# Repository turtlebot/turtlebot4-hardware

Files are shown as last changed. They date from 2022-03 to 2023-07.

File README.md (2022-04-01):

# Turtlebot4 Hardware

<table>
    <thead>
        <tr>
            <th>Feature</th>
            <th>
                TurtleBot 4 Lite
            </th>
            <th>
                TurtleBot 4
            </th>
        </tr>
    </thead>
    <tbody>
        <tr>
            <td>Size (L x W x H)</td>
            <td>342 x 339 x 192 mm</td>
            <td>342 x 339 x 351 mm</td>
        </tr>
        <tr>
            <td>Weight</td>
            <td>3270 g</td>
            <td>3945 g</td>
        </tr>
        <tr>
            <td>Base platform</td>
            <td>iRobot® Create® 3</td>
            <td>iRobot® Create® 3</td>
        </tr>
        <tr>
            <td>Wheels (Diameter)</td>
            <td>72 mm</td>
            <td>72 mm</td>
        </tr>
        <tr>
            <td>Ground Clearance</td>
            <td>4.5 mm</td>
            <td>4.5 mm</td>
        </tr>
        <tr>
            <td>On-board Computer</td>
            <td>Raspberry Pi 4B 4GB</td>
            <td>Raspberry Pi 4B 4GB</td>
        </tr>
        <tr>
            <td>Maximum linear velocity	</td>
            <td>0.31 m/s in safe mode, 0.46 m/s without safe mode</td>
            <td>0.31 m/s in safe mode, 0.46 m/s without safe mode</td>
        </tr>
        <tr>
            <td>Maximum angular velocity</td>
            <td>1.90 rad/s</td>
            <td>1.90 rad/s</td>
        </tr>
        <tr>
            <td>Maximum payload	</td>
            <td>9 kg</td>
            <td>9 kg</td>
        </tr>
        <tr>
            <td>Operation time	</td>
            <td>2h 30m - 4h depending on load</td>
            <td>2h 30m - 4h depending on load</td>
        </tr>
        <tr>
            <td>Charging time</td>
            <td>2h 30m</td>
            <td>2h 30m</td>
        </tr>
        <tr>
            <td>Bluetooth Controller</td>
            <td>Not Included</td>
            <td>TurtleBot 4 Controller</td>
        </tr>
        <tr>
            <td>Lidar</td>
            <td>RPLIDAR A1M8</td>
            <td>RPLIDAR A1M8</td>
        </tr>
        <tr>
            <td>Camera</td>
            <td>OAK-D-Lite</td>
            <td>OAK-D-Pro</td>
        </tr>
        <tr>
            <td>User Power</td>
            <td>
                VBAT @1.9A <br/>
                5V @ Low current <br/>
                3.3V @ Low current
            </td>
            <td>
                VBAT @ 300 mA <br/>
                12V @ 300 mA <br/>
                5V @ 500 mA <br/>
                3.3v @ 250 mA
            </td>
        </tr>
        <tr>
            <td>USB Expansion</td>
            <td>
                USB 2.0 (Type A) x2 <br/>
                USB 3.0 (Type A) x2
            </td>
            <td>
                USB 2.0 (Type A) x2 <br/>
                USB 3.0 (Type A) x1 <br/>
                USB 3.0 (Type C) x4
            </td>
        </tr>
        <tr>
            <td>Programmable LEDs</td>
            <td>Create® 3 Lightring</td>
            <td>
                Create® 3 Lightring <br/>
                User LED x2
            </td>
        </tr>
        <tr>
            <td>Status LEDs</td>
            <td>-</td>
            <td>
                Power LED <br/>
                Motors LED <br/>
                WiFi LED <br/>
                Comms LED <br/>
                Battery LED
            </td>
        </tr>
        <tr>
            <td>Buttons and Switches</td>
            <td>
                Create® 3 User buttons x2 <br/>
                Create® 3 Power Button x1
            </td>
            <td>
                Create® 3 User buttons x2 <br/>
                Create® 3 Power Button x1 <br/>
                User Buttons x4
            </td>
        </tr>
        <tr>
            <td>Battery</td>
            <td>26 Wh Lithium Ion (14.4V nominal)</td>
            <td>26 Wh Lithium Ion (14.4V nominal)</td>
        </tr>
        <tr>
            <td>Charging Dock</td>
            <td>Included</td>
            <td>Included</td>
        </tr>
    </tbody>
</table>

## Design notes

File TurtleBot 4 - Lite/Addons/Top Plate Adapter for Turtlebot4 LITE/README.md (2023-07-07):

# Top Plate Adapter for Turtlebot4 LITE

These adapter plates allow easy attachment of additional components without making permanent modificaitons to the Create3 base. This adapter plate has been designed to be compatible with the Turtlebot4 Standard Top Plate. The fastener locations can be altered as needed.

Use of this adapter plate requires some additional hardware components. Suggested hardware is linked from Mcmaster Carr but substitutions that match the part specifications will work as well. 

# Component List

| Description | Quantity | Mcmaster Carr Equivalent |
|:---|:---|---|
| Threaded Insert, Heat Set—M4×0.7 8mm Long, Brass | 4 | 94180A353 |
| Screw, Cap, Round Head—M3×0.5 X 10, Stainless Steel Type 18-8 | 4 | 92095A182 |
| Nut, Hex—M3×0.5, Stainless Steel Type 18-8 | 4 | 91828A211 |
| Washer, Flat—Ø3.2 X Ø7 X 0.6, Stainless Steel Type 18-8 | 4 | 93475A210 |

installed_adapter_plate

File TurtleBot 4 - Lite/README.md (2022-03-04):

# Turtlebot4 Lite

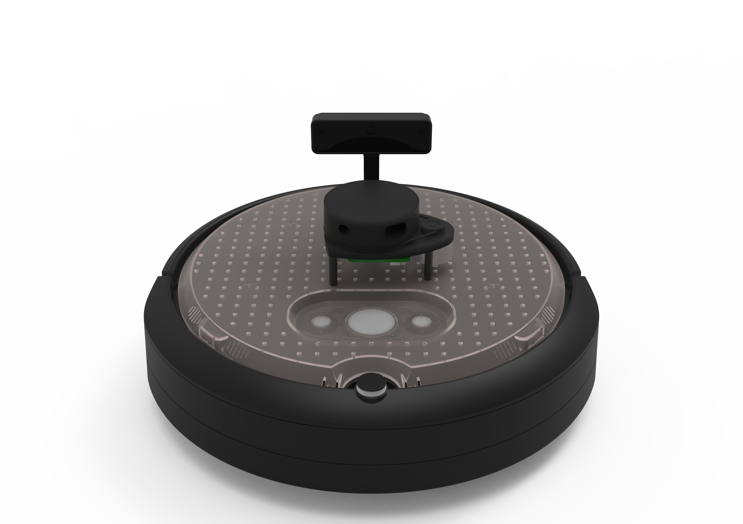
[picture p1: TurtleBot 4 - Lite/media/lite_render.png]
turtlebot4_lite


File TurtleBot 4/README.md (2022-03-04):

# Turtlebot4

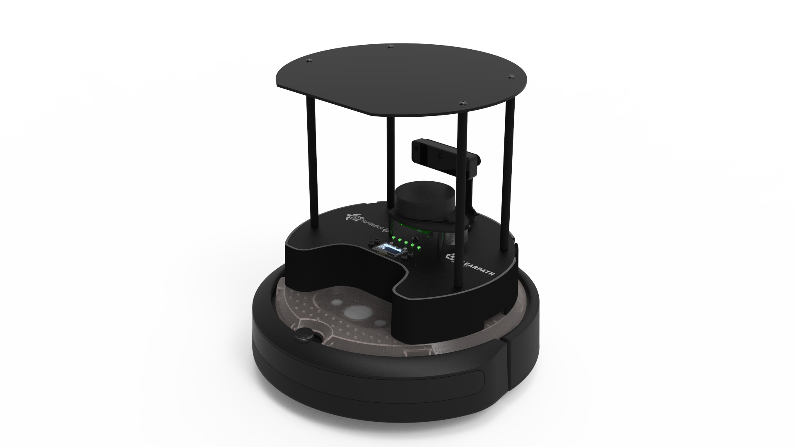
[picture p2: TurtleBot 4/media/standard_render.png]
turtlebot4_standard


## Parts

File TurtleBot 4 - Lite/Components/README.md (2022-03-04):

# Components

[025963 - OAK-D-Lite, Luxonis](https://github.com/luxonis/depthai-hardware/tree/master/DM9095_OAK-D-LITE_DepthAI_USB3C)

[025962 - LIDAR, RPLidar A1M8, Slamtec](https://github.com/turtlebot/turtlebot4-hardware/tree/master/TurtleBot%204/Components/025962%20-%20LIDAR%2C%20RPLidar%20A1M8%2C%20Slamtec)

[025426 - BRACKET, CAMERA, ALUMINIUM ALLOY](https://github.com/turtlebot/turtlebot4-hardware/tree/master/TurtleBot%204/Components/025426%20-%20BRACKET%2C%20CAMERA%2C%20ALUMINIUM%20ALLOY)

[025552 - STANDOFF, THREADED, HEX—MALE-FEMALE, M2_5 X 5, HEX SIZE 4_5MM, ALUMINUM](https://github.com/turtlebot/turtlebot4-hardware/tree/master/TurtleBot%204/Components/025552%20-%20STANDOFF%2C%20THREADED%2C%20HEX%E2%80%94MALE-FEMALE%2C%20M2_5%20X%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)

## USB Cables

[025941 - Cable, USB 3.0 USB-C 90° Male to USB-A Male, 300mm](https://github.com/turtlebot/turtlebot4-hardware/tree/master/TurtleBot%204/Components/USB%20Cables/025941%20-%20Cable%2C%20USB%203.0%20USB-C%2090%C2%B0%20Male%20to%2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)

[025942 - Cable, USB 3.0 USB-C Male to USB-C 90° Male, 300mm](https://github.com/turtlebot/turtlebot4-hardware/tree/master/TurtleBot%204/Components/USB%20Cables/025942%20-%20Cable%2C%20USB%203.0%20USB-C%20Male%20to%20USB-C%2090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)

[025944 - Cable, USB 2.0 Micro-B Male to USB-A Male, 300mm](https://github.com/turtlebot/turtlebot4-hardware/tree/master/TurtleBot%204/Components/USB%20Cables/025944%20-%20Cable%2C%20USB%202.0%20Micro-B%20Male%20to%20USB-A%20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)

# Fastener List

| CPR Part Number | Description | Quantity | Mcmaster Carr Equivalent |
|:---|:---|:---|---|
| 10898 | Nut, Hex—M4×0.7, Stainless Steel Type 18-8 | 3 | 91828A231 |
| 25552 | Standoff, Threaded, Hex - Male-Female, M2.5 X 5, Hex Size 4.5 mm, Aluminum | 4 | 98952A101 |
| 25609 | Screw, Cap, Round Head—M4×0.7 X 10, Stainless Steel Type 18-8, Black Oxide | 5 | 97763A817 |
| 25610 | Washer, Flat—Ø4.3 X Ø9 X 0.9, Stainless Steel, Black Oxide | 5 | 98269A430 |
| 25616 | Screw, Cap, Round Head—M2.5×0.45 X 4, Stainless Steel Type 18-8, Black Oxide | 4 | 97763A412 |
| 25740 | Nut, Hex—M2.5 × 0.45 X 2.1, Steel Class 4, Zinc Plate | 4 | 90695A031 |
| 26387 | Washer, Locking, Split—DIN 7980 M4 X 1.1, Steel, Black | 2 | 91190A520 |
| 26634 | Screw, Cap, Round Head—M2.5×0.45 X 6, Stainless Steel Type 316 | 4 | 94500A213 |
| 26649 | Tape, Double-Sided, 3M VHB 4959 —1/2" X 0.12", White | 20mm | 75935A28 |

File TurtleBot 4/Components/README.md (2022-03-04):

# Components

[025961 - OAK-D-Pro, Luxonis](https://github.com/luxonis/depthai-hardware/tree/master/DM9098_OAK-D-Pro)

# Fastener List

| CPR Part Number | Description | Quantity | Mcmaster Carr Equivalent |
|:---|:---|:---|---|
| 10898 | Nut, Hex—M4×0.7, Stainless Steel Type 18-8 | 3 | 91828A231 |
| 25552 | Standoff, Threaded, Hex - Male-Female, M2.5 X 5, Hex Size 4.5 mm, Aluminum | 4 | 98952A101 |
| 25609 | Screw, Cap, Round Head—M4×0.7 X 10, Stainless Steel Type 18-8, Black Oxide | 10 | 97763A817 |
| 25610 | Washer, Flat—Ø4.3 X Ø9 X 0.9, Stainless Steel, Black Oxide | 5 | 98269A430 |
| 25614 | Screw, Cap, Flat Head—M3.5 X 10, Steal, Zinc Plate | 8 | 98269A430 |
| 25616 | Screw, Cap, Round Head—M2.5×0.45 X 4, Stainless Steel Type 18-8, Black Oxide | 4 | 97763A412 |
| 25740 | Nut, Hex—M2.5 × 0.45 X 2.1, Steel Class 4, Zinc Plate | 4 | 90695A031 |
| 26387 | Washer, Locking, Split—DIN 7980 M4 X 1.1, Steel, Black | 2 | 91190A520 |
| 26634 | Screw, Cap, Round Head—M2.5×0.45 X 6, Stainless Steel Type 316 | 4 | 94500A213 |
| 26649 | Tape, Double-Sided, 3M VHB 4959 —1/2" X 0.12", White | 20mm | 75935A28 |

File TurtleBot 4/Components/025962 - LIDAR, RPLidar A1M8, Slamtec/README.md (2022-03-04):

# RPLIDAR A1M8

Product page: https://www.slamtec.com/en/Lidar/A1

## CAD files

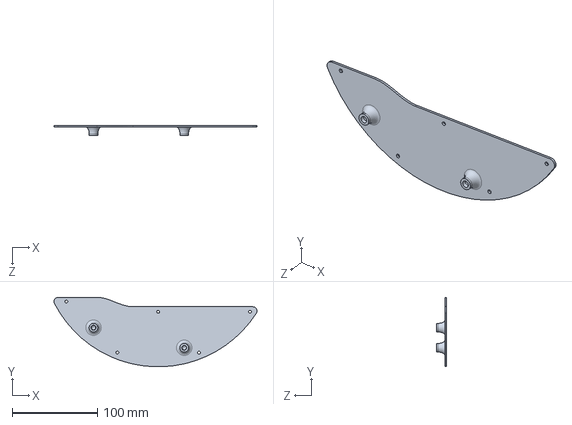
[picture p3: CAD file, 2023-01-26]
TurtleBot 4 - Lite/Addons/Top Plate Adapter for Turtlebot4 LITE/Adapter Plate, Turtlebot4 Lite, Right Side—Plastic, 3D Printed.SLDPRT
238.8 x 81.5 x 12.0 mm

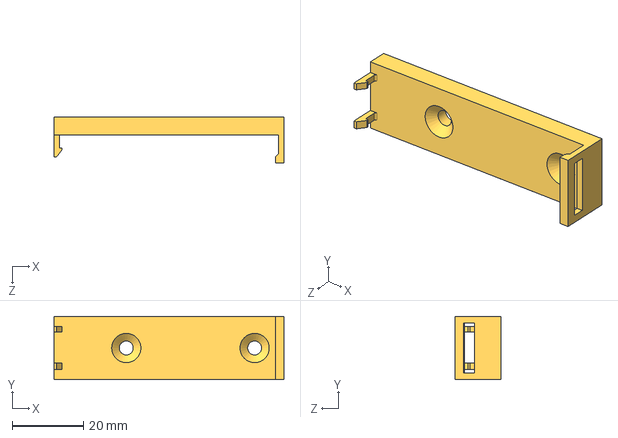
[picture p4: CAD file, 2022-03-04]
TurtleBot 4/Addons/Teensy 4.1 Adapter/Clearpath Robotics Teensy Mount.STEP
64.5 x 17.8 x 12.8 mm

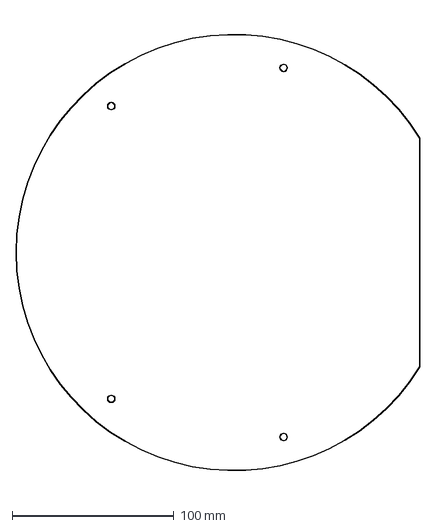
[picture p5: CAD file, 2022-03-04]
TurtleBot 4/Components/025394 - PLATE, SENSOR INTEGRATION/025394-FLAT_3.DXF
250.0 x 292.7 mm

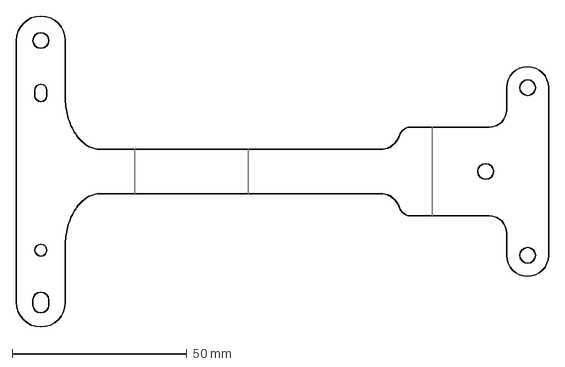
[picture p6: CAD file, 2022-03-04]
TurtleBot 4/Components/025426 - BRACKET, CAMERA, ALUMINIUM ALLOY/025426-FLAT_6.DXF
152.4 x 89.0 mm

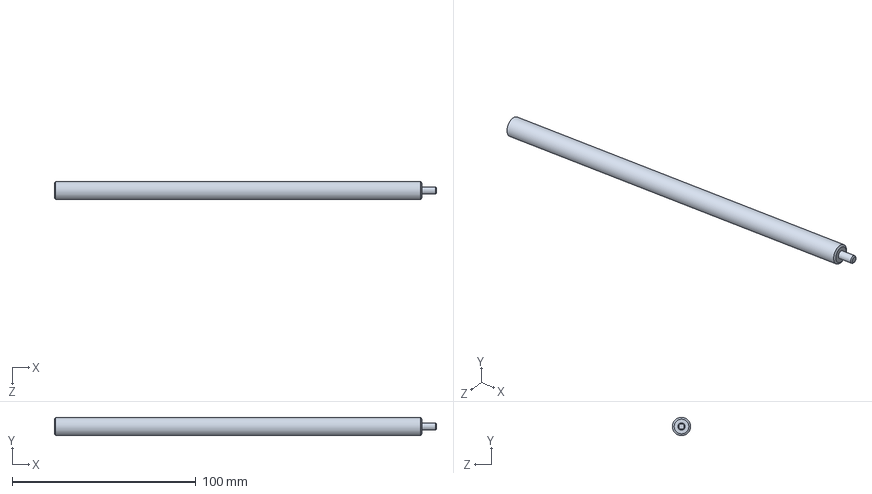
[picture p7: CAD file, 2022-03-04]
TurtleBot 4/Components/025481 - STANDOFF, THREADED, ROUND—MALE-FEMALE, M4 X 200, ALUMINUM/025481-GEO_4.STEP
208.0 x 10.0 x 10.0 mm

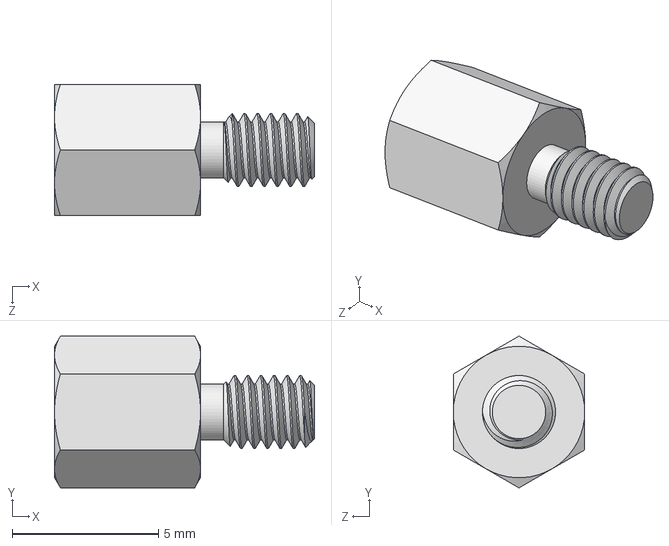
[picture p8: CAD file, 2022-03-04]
TurtleBot 4/Components/025552 - STANDOFF, THREADED, HEX—MALE-FEMALE, M2_5 X 5, HEX SIZE 4_5MM, ALUMINUM/025552-GEO_2.STEP
8.90 x 5.20 x 4.50 mm

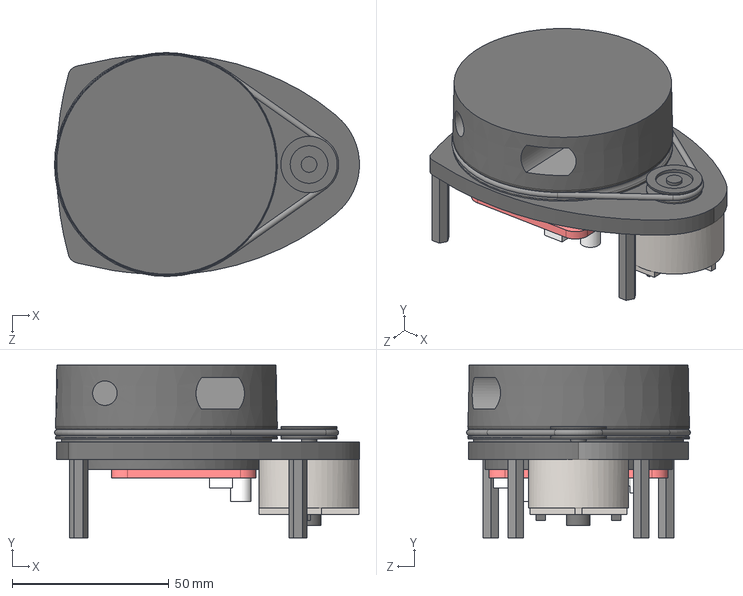
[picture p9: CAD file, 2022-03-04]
TurtleBot 4/Components/025962 - LIDAR, RPLidar A1M8, Slamtec/025962-GEO_1 - LIDAR, RPLidar A1M8, Slamtec.STEP
97.3 x 55.1 x 71.4 mm

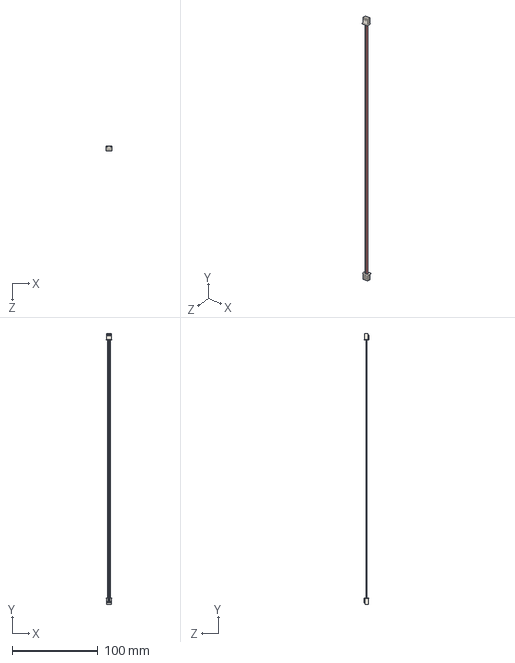
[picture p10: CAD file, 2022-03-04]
TurtleBot 4/Components/Power Cable/026211-GEO_2.STEP
7.30 x 315.5 x 6.00 mm
XHP-2_Item Name from PLM x 2
22AWG, 300mm Wires - Red, Black_Item Name from PLM

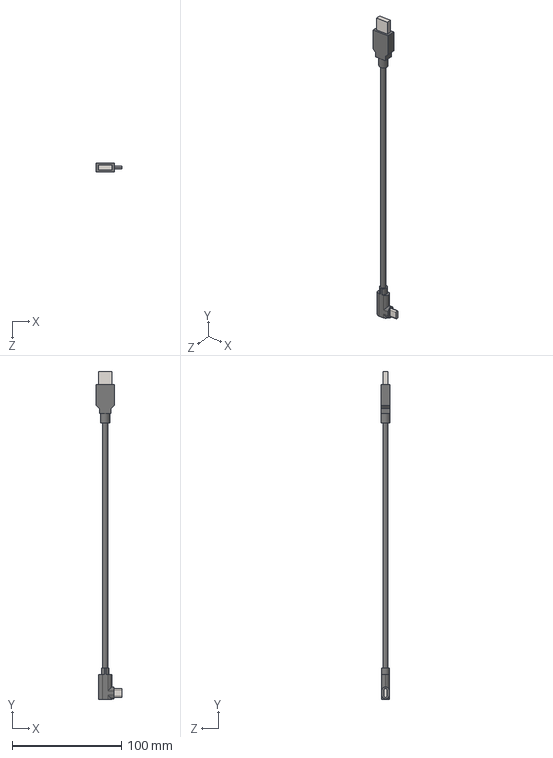
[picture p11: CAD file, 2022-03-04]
TurtleBot 4/Components/USB Cables/025941 - Cable, USB 3.0 USB-C 90° Male to USB-A Male, 300mm/025941-GEO_2.STEP
23.4 x 300.0 x 8.45 mm

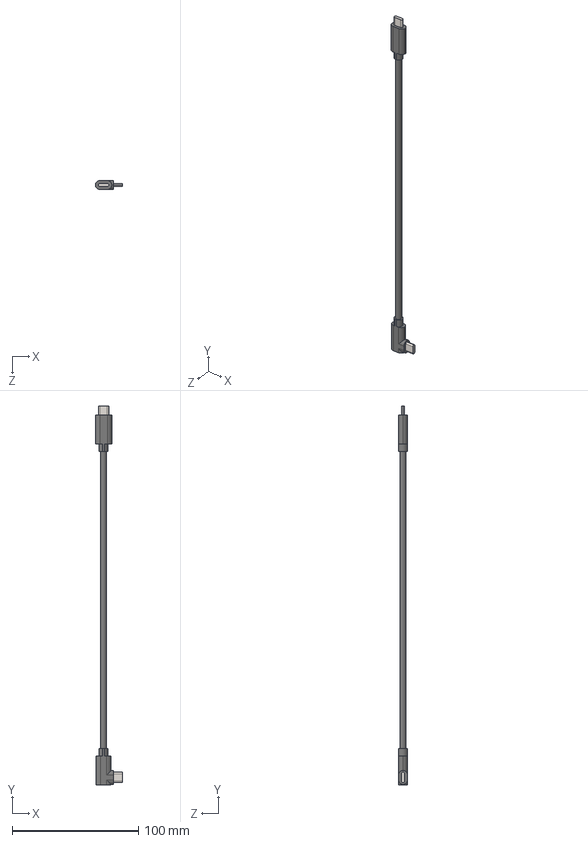
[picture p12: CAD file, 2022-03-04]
TurtleBot 4/Components/USB Cables/025942 - Cable, USB 3.0 USB-C Male to USB-C 90° Male, 300mm/025942-GEO_1.STEP
21.6 x 300.0 x 7.00 mm

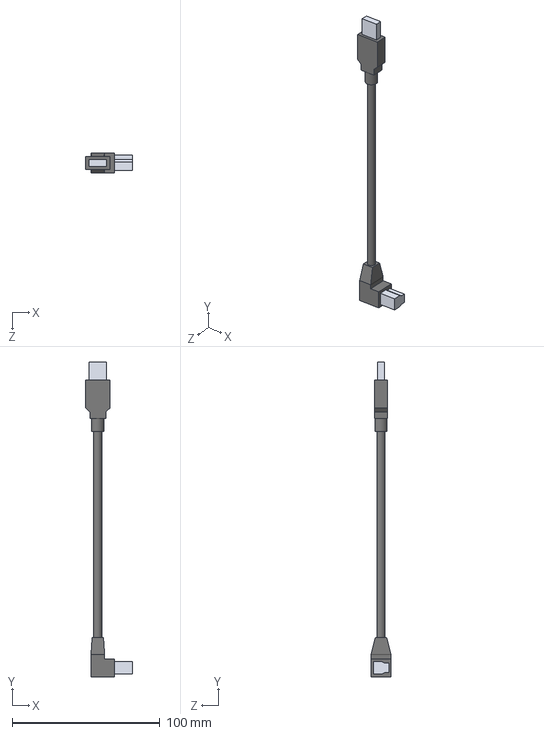
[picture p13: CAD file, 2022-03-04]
TurtleBot 4/Components/USB Cables/025943 - Cable, USB 3.0 USB-B 90° Male to USB-A Male, 200mm/025943-GEO_1.STEP
31.6 x 212.9 x 13.5 mm

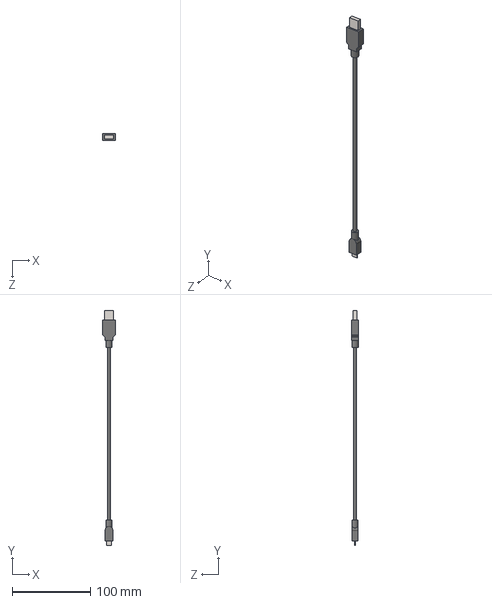
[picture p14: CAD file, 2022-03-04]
TurtleBot 4/Components/USB Cables/025944 - Cable, USB 2.0 Micro-B Male to USB-A Male, 300mm/025944-GEO_2.STEP
16.5 x 300.0 x 8.45 mm

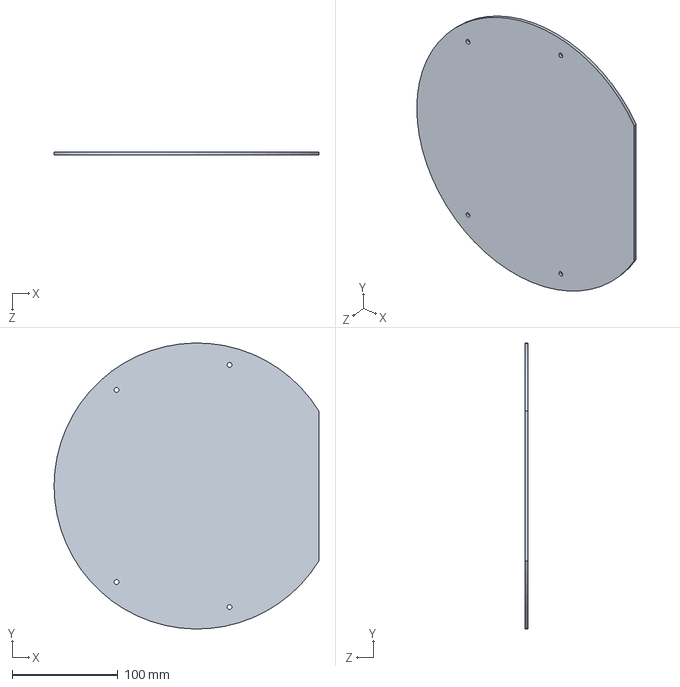
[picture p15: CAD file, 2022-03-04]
TurtleBot 4/Components/025394 - PLATE, SENSOR INTEGRATION/025394-GEO_3.STEP
250.0 x 270.0 x 3.00 mm

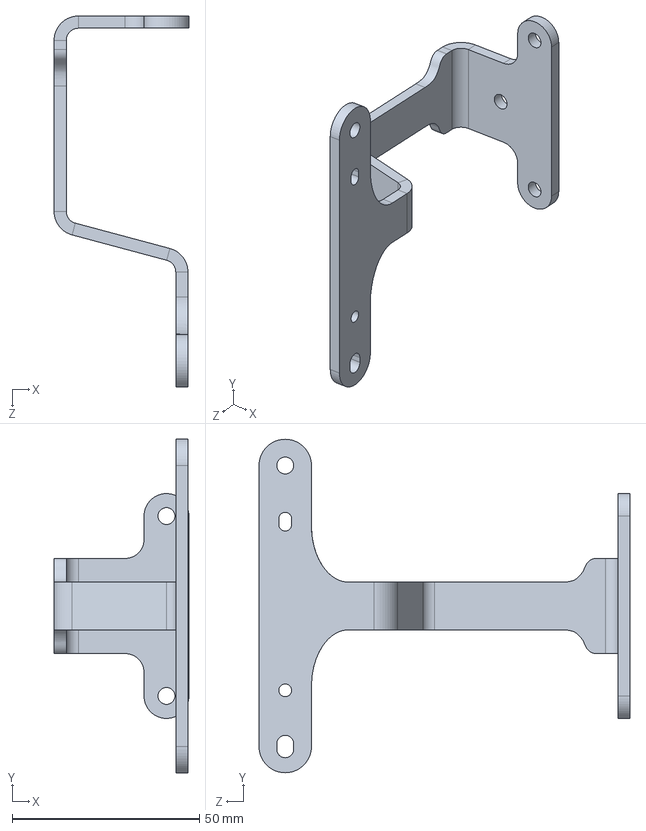
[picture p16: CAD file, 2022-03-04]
TurtleBot 4/Components/025426 - BRACKET, CAMERA, ALUMINIUM ALLOY/025426-GEO_6.STEP
36.0 x 89.0 x 99.0 mm

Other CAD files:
TurtleBot 4 - Lite/Addons/Top Plate Adapter for Turtlebot4 LITE/Adapter Plate, Turtlebot4 Lite, Left Side—Plastic, 3D Printed.SLDPRT
TurtleBot 4 - Lite/Addons/Top Plate Adapter for Turtlebot4 LITE/Adapter Plate, Turtlebot4 Lite, Left Side—Plastic, 3D Printed.STL
TurtleBot 4 - Lite/Addons/Top Plate Adapter for Turtlebot4 LITE/Adapter Plate, Turtlebot4 Lite, Right Side—Plastic, 3D Printed.STL

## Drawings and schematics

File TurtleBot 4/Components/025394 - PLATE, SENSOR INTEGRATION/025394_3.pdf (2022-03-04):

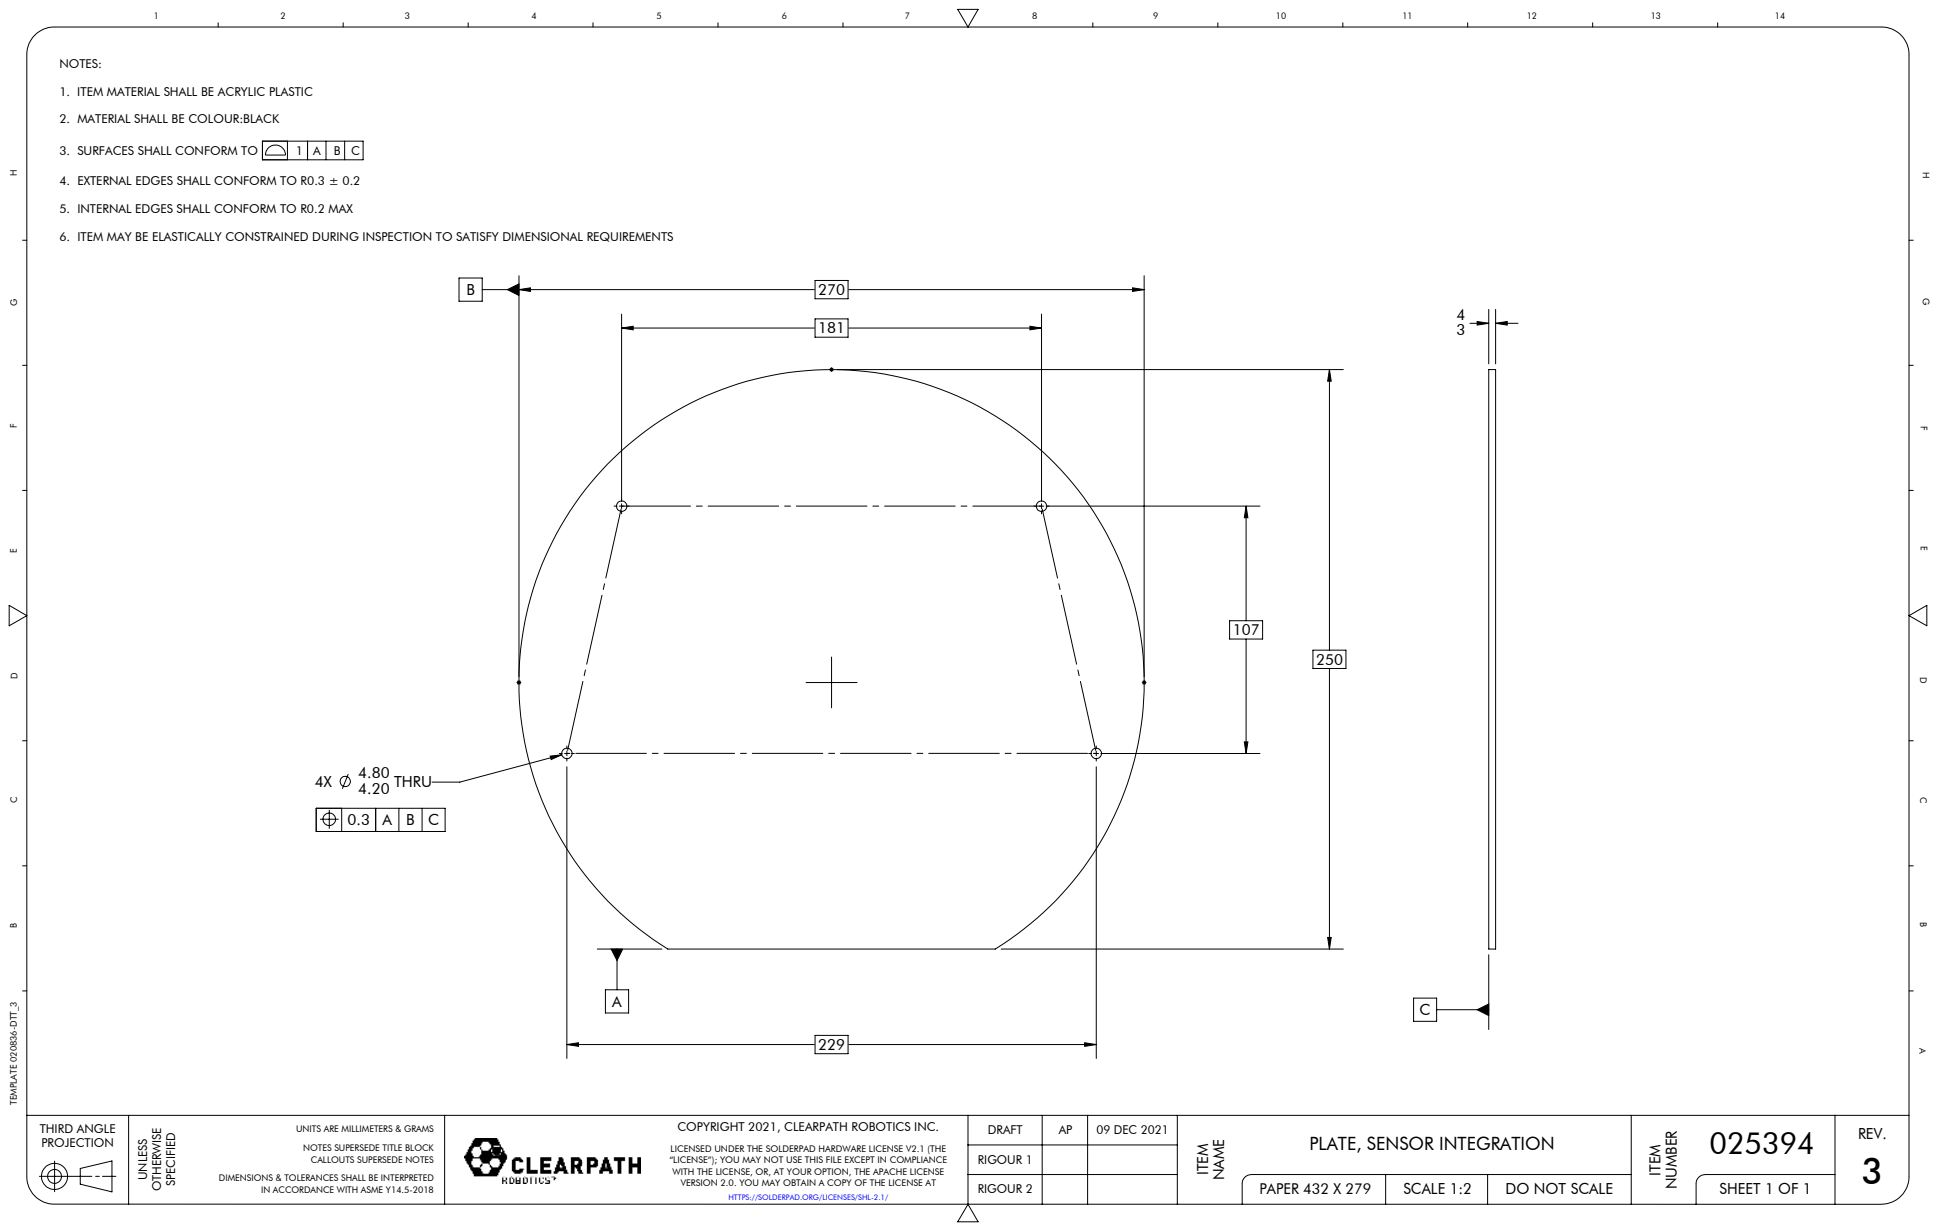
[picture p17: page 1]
4.20 THRU; 3. SURFACES SHALL CONFORM TO; SCALE 1:2; SHEET 1 OF 1; THIRD ANGLE; PAPER 432 X 279; PLATE, SENSOR INTEGRATION; 025394 DRAFT; RIGOUR 1; RIGOUR 2; 09 DEC 2021; TEMPLATE 020836-DTT_3; IN ACCORDANCE WITH ASME Y14.5-2018; DO NOT SCALE

NOTES:
1. ITEM MATERIAL SHALL BE ACRYLIC PLASTIC
2. MATERIAL SHALL BE COLOUR:BLACK

4. EXTERNAL EDGES SHALL CONFORM TO R0.3 ± 0.2
5. INTERNAL EDGES SHALL CONFORM TO R0.2 MAX
6. ITEM MAY BE ELASTICALLY CONSTRAINED DURING INSPECTION TO SATISFY DIMENSIONAL REQUIREMENTS

UNITS ARE MILLIMETERS & GRAMS
NOTES SUPERSEDE TITLE BLOCK
CALLOUTS SUPERSEDE NOTES

COPYRIGHT 2021, CLEARPATH ROBOTICS INC.

LICENSED UNDER THE SOLDERPAD HARDWARE LICENSE V2.1 (THE
“LICENSE”); YOU MAY NOT USE THIS FILE EXCEPT IN COMPLIANCE
WITH THE LICENSE, OR, AT YOUR OPTION, THE APACHE LICENSE
VERSION 2.0. YOU MAY OBTAIN A COPY OF THE LICENSE AT

DIMENSIONS & TOLERANCES SHALL BE INTERPRETED

HTTPS://SOLDERPAD.ORG/LICENSES/SHL-2.1/

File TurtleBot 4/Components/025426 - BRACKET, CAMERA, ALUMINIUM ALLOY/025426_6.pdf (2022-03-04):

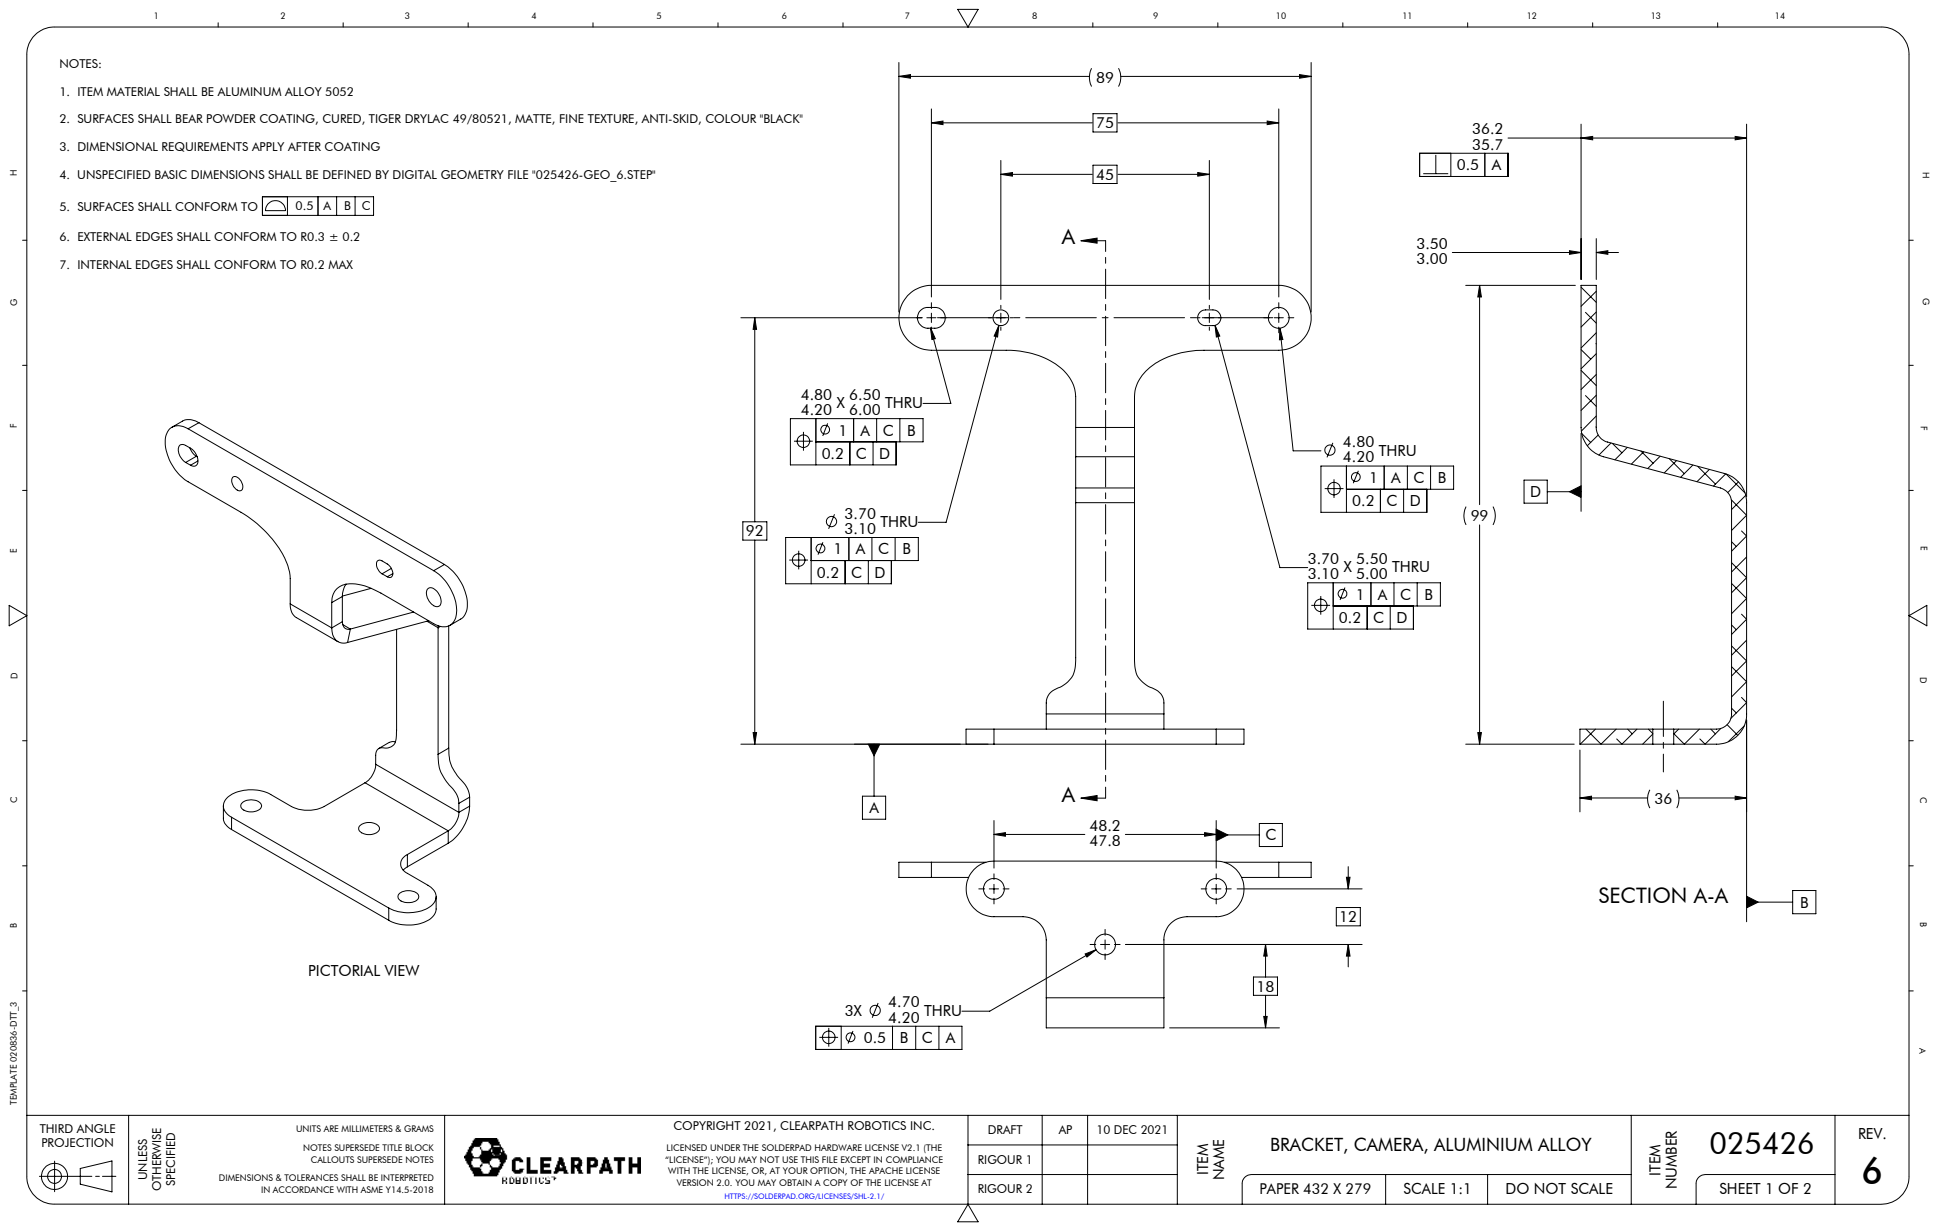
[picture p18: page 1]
3.10 THRU; 4.20 THRU; 4.20 X 6.50 6.00 THRU; 3.10 X 5.50 5.00 THRU; SECTION A-A; 5. SURFACES SHALL CONFORM TO; PICTORIAL VIEW; SCALE 1:1; SHEET 1 OF 2; THIRD ANGLE; PAPER 432 X 279; BRACKET, CAMERA, ALUMINIUM ALLOY; 025426 DRAFT; RIGOUR 1; RIGOUR 2; 10 DEC 2021; TEMPLATE 020836-DTT_3; IN ACCORDANCE WITH ASME Y14.5-2018; DO NOT SCALE

NOTES:
1. ITEM MATERIAL SHALL BE ALUMINUM ALLOY 5052
2. SURFACES SHALL BEAR POWDER COATING, CURED, TIGER DRYLAC 49/80521, MATTE, FINE TEXTURE, ANTI-SKID, COLOUR "BLACK"
3. DIMENSIONAL REQUIREMENTS APPLY AFTER COATING
4. UNSPECIFIED BASIC DIMENSIONS SHALL BE DEFINED BY DIGITAL GEOMETRY FILE "025426-GEO_6.STEP"

6. EXTERNAL EDGES SHALL CONFORM TO R0.3 ± 0.2
7. INTERNAL EDGES SHALL CONFORM TO R0.2 MAX

0.2 | C | D

UNITS ARE MILLIMETERS & GRAMS
NOTES SUPERSEDE TITLE BLOCK
CALLOUTS SUPERSEDE NOTES

COPYRIGHT 2021, CLEARPATH ROBOTICS INC.

LICENSED UNDER THE SOLDERPAD HARDWARE LICENSE V2.1 (THE
“LICENSE”); YOU MAY NOT USE THIS FILE EXCEPT IN COMPLIANCE
WITH THE LICENSE, OR, AT YOUR OPTION, THE APACHE LICENSE
VERSION 2.0. YOU MAY OBTAIN A COPY OF THE LICENSE AT

DIMENSIONS & TOLERANCES SHALL BE INTERPRETED

HTTPS://SOLDERPAD.ORG/LICENSES/SHL-2.1/

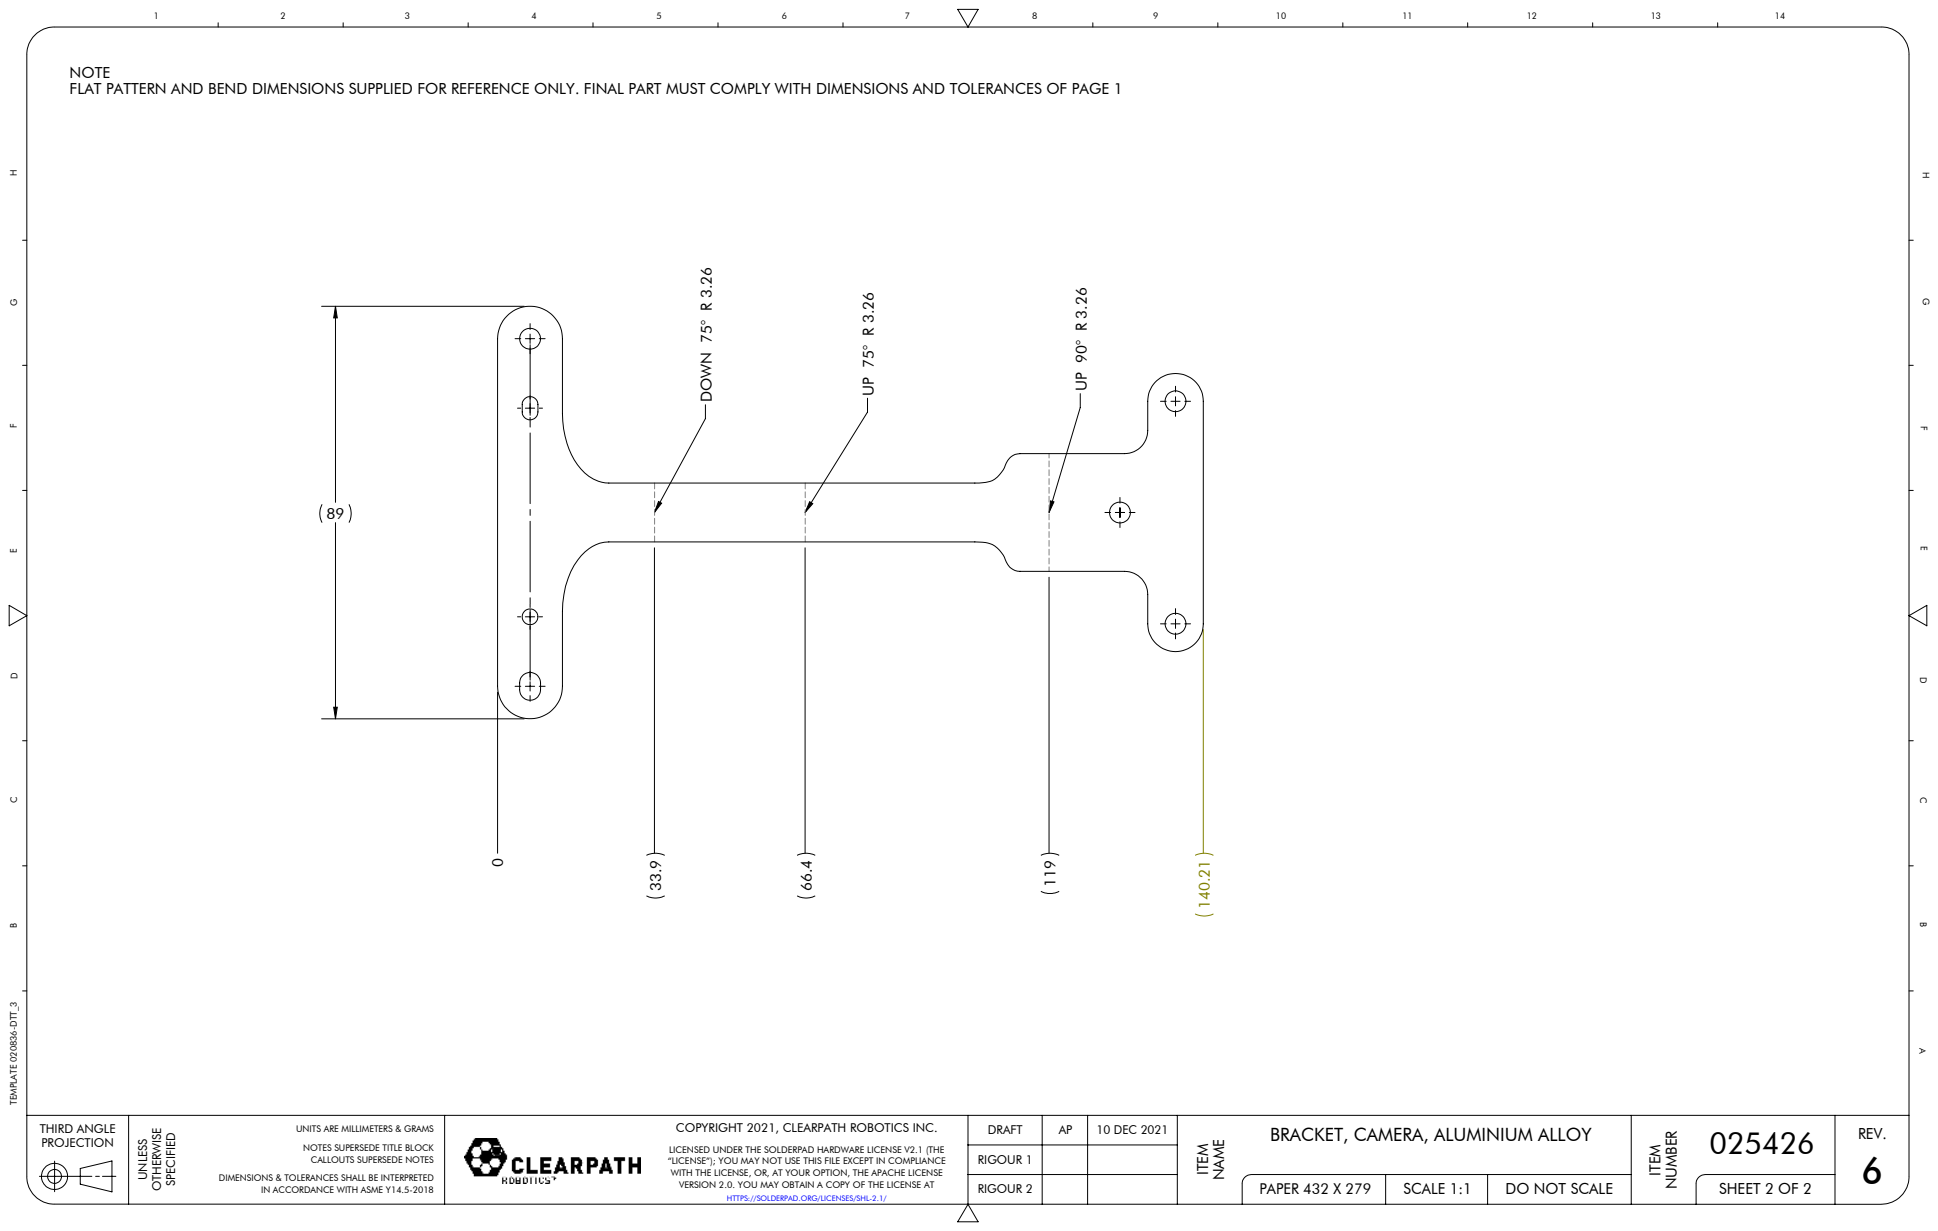
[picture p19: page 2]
DOWN 75° R 3.26; SCALE 1:1; SHEET 2 OF 2; THIRD ANGLE; PAPER 432 X 279; RIGOUR 1; RIGOUR 2; 10 DEC 2021; TEMPLATE 020836-DTT_3; IN ACCORDANCE WITH ASME Y14.5-2018; DO NOT SCALE

NOTE
FLAT PATTERN AND BEND DIMENSIONS SUPPLIED FOR REFERENCE ONLY. FINAL PART MUST COMPLY WITH DIMENSIONS AND TOLERANCES OF PAGE 1

UNITS ARE MILLIMETERS & GRAMS
NOTES SUPERSEDE TITLE BLOCK
CALLOUTS SUPERSEDE NOTES

COPYRIGHT 2021, CLEARPATH ROBOTICS INC.

025426 BRACKET, CAMERA, ALUMINIUM ALLOY DRAFT

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

DIMENSIONS & TOLERANCES SHALL BE INTERPRETED

HTTPS://SOLDERPAD.ORG/LICENSES/SHL-2.1/

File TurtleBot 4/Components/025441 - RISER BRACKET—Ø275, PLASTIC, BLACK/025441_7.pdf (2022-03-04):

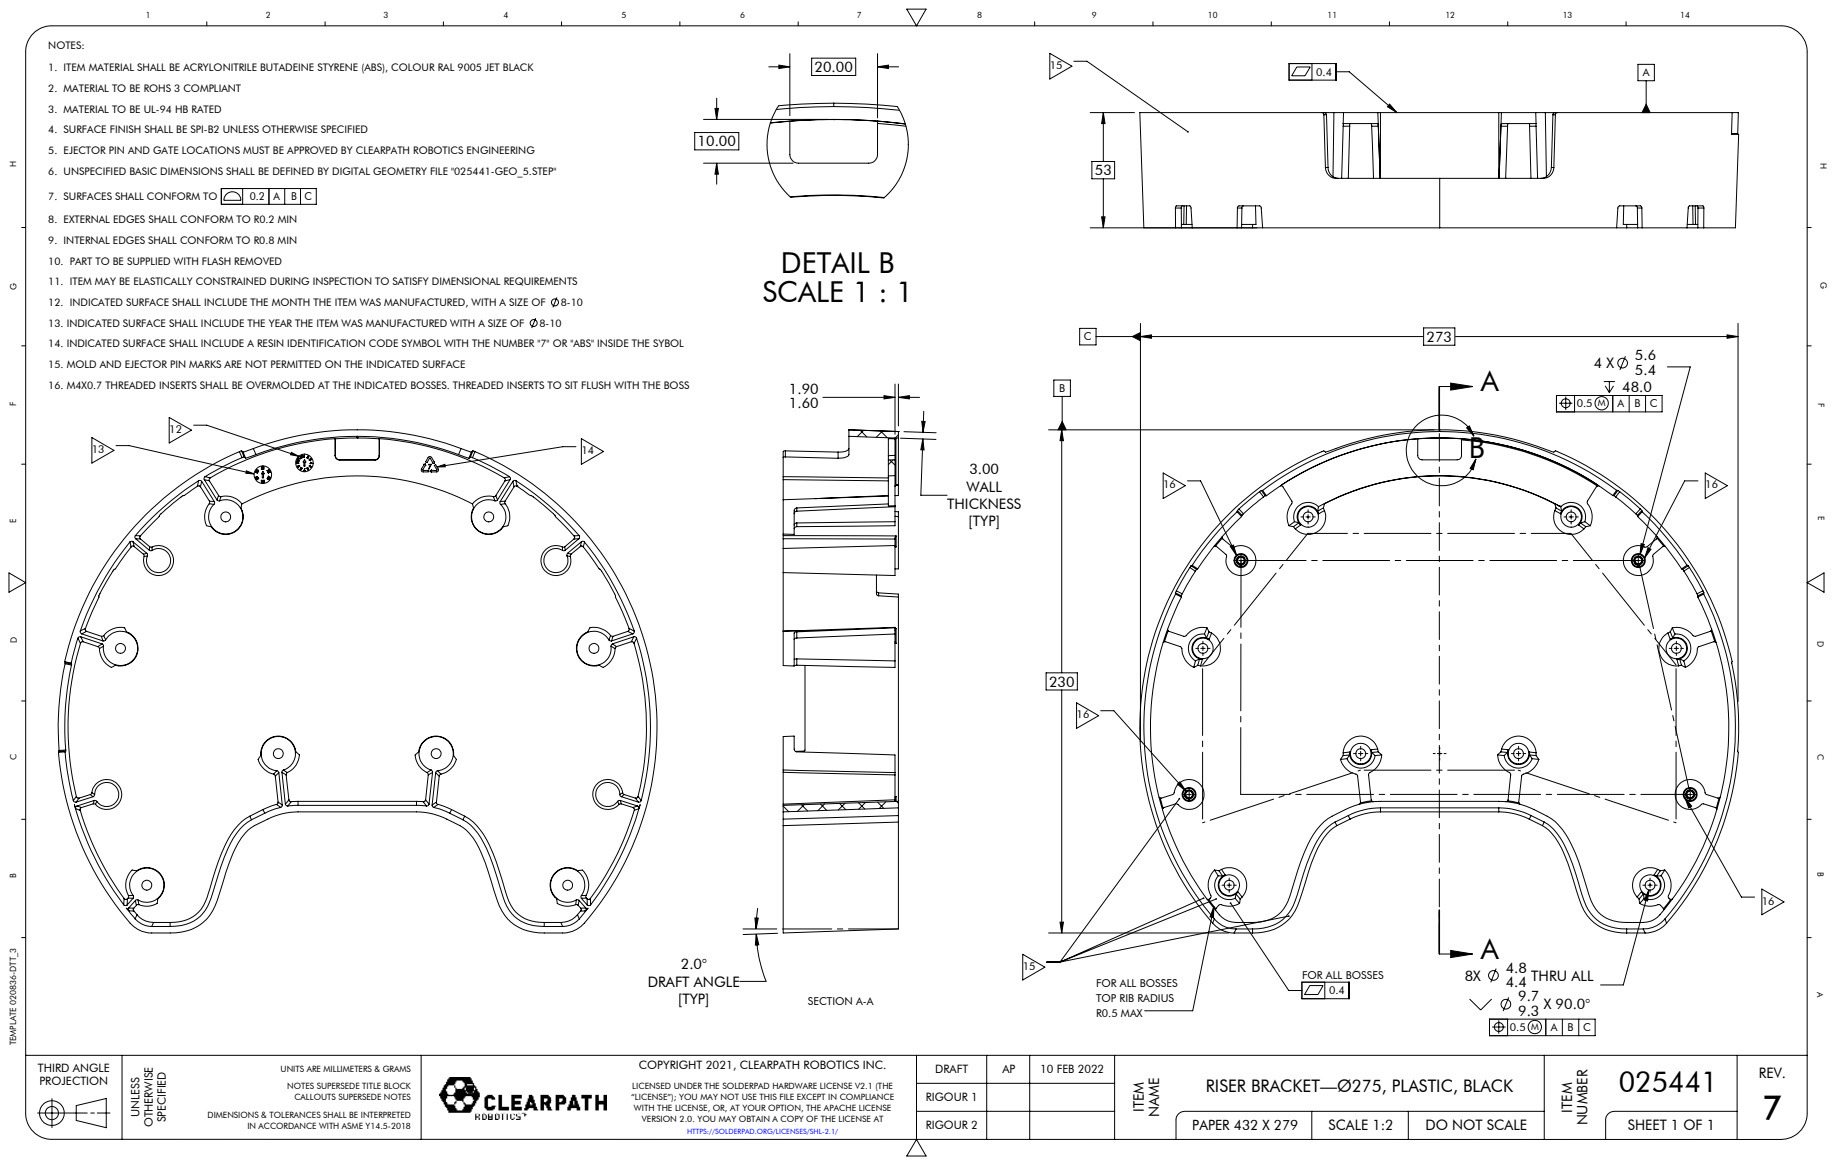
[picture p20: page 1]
4.4 THRU ALL; NOT TO SCALE; DRAFT ANGLE; [TYP]; SECTION A-A; DETAIL B SCALE 1 : 1; 7. SURFACES SHALL CONFORM TO; SCALE 1:2; SHEET 1 OF 1; THIRD ANGLE; PAPER 432 X 279; RISER BRACKET—Ø275, PLASTIC, BLACK; 025441 DRAFT; RIGOUR 1; RIGOUR 2; 10 FEB 2022; TEMPLATE 020836-DTT_3; IN ACCORDANCE WITH ASME Y14.5-2018; DO NOT SCALE

NOTES:
1. ITEM MATERIAL SHALL BE ACRYLONITRILE BUTADEINE STYRENE (ABS), COLOUR RAL 9005 JET BLACK
2. MATERIAL TO BE ROHS 3 COMPLIANT
3. MATERIAL TO BE UL-94 HB RATED
4. SURFACE FINISH SHALL BE SPI-B2 UNLESS OTHERWISE SPECIFIED
5. EJECTOR PIN AND GATE LOCATIONS MUST BE APPROVED BY CLEARPATH ROBOTICS ENGINEERING
6. UNSPECIFIED BASIC DIMENSIONS SHALL BE DEFINED BY DIGITAL GEOMETRY FILE "025441-GEO_5.STEP"

8. EXTERNAL EDGES SHALL CONFORM TO R0.2 MIN
9. INTERNAL EDGES SHALL CONFORM TO R0.8 MIN
10. PART TO BE SUPPLIED WITH FLASH REMOVED
11. ITEM MAY BE ELASTICALLY CONSTRAINED DURING INSPECTION TO SATISFY DIMENSIONAL REQUIREMENTS
12. INDICATED SURFACE SHALL INCLUDE THE MONTH THE ITEM WAS MANUFACTURED, WITH A SIZE OF 8-10
13. INDICATED SURFACE SHALL INCLUDE THE YEAR THE ITEM WAS MANUFACTURED WITH A SIZE OF 8-10
14. INDICATED SURFACE SHALL INCLUDE A RESIN IDENTIFICATION CODE SYMBOL WITH THE NUMBER "7" OR "ABS" INSIDE THE SYBOL
15. MOLD AND EJECTOR PIN MARKS ARE NOT PERMITTED ON THE INDICATED SURFACE
16. M4X0.7 THREADED INSERTS SHALL BE OVERMOLDED AT THE INDICATED BOSSES. THREADED INSERTS TO SIT FLUSH WITH THE BOSS

FOR ALL BOSSES
TOP RIB RADIUS
R0.5 MAX

UNITS ARE MILLIMETERS & GRAMS
NOTES SUPERSEDE TITLE BLOCK
CALLOUTS SUPERSEDE NOTES

COPYRIGHT 2021, CLEARPATH ROBOTICS INC.

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

DIMENSIONS & TOLERANCES SHALL BE INTERPRETED

HTTPS://SOLDERPAD.ORG/LICENSES/SHL-2.1/

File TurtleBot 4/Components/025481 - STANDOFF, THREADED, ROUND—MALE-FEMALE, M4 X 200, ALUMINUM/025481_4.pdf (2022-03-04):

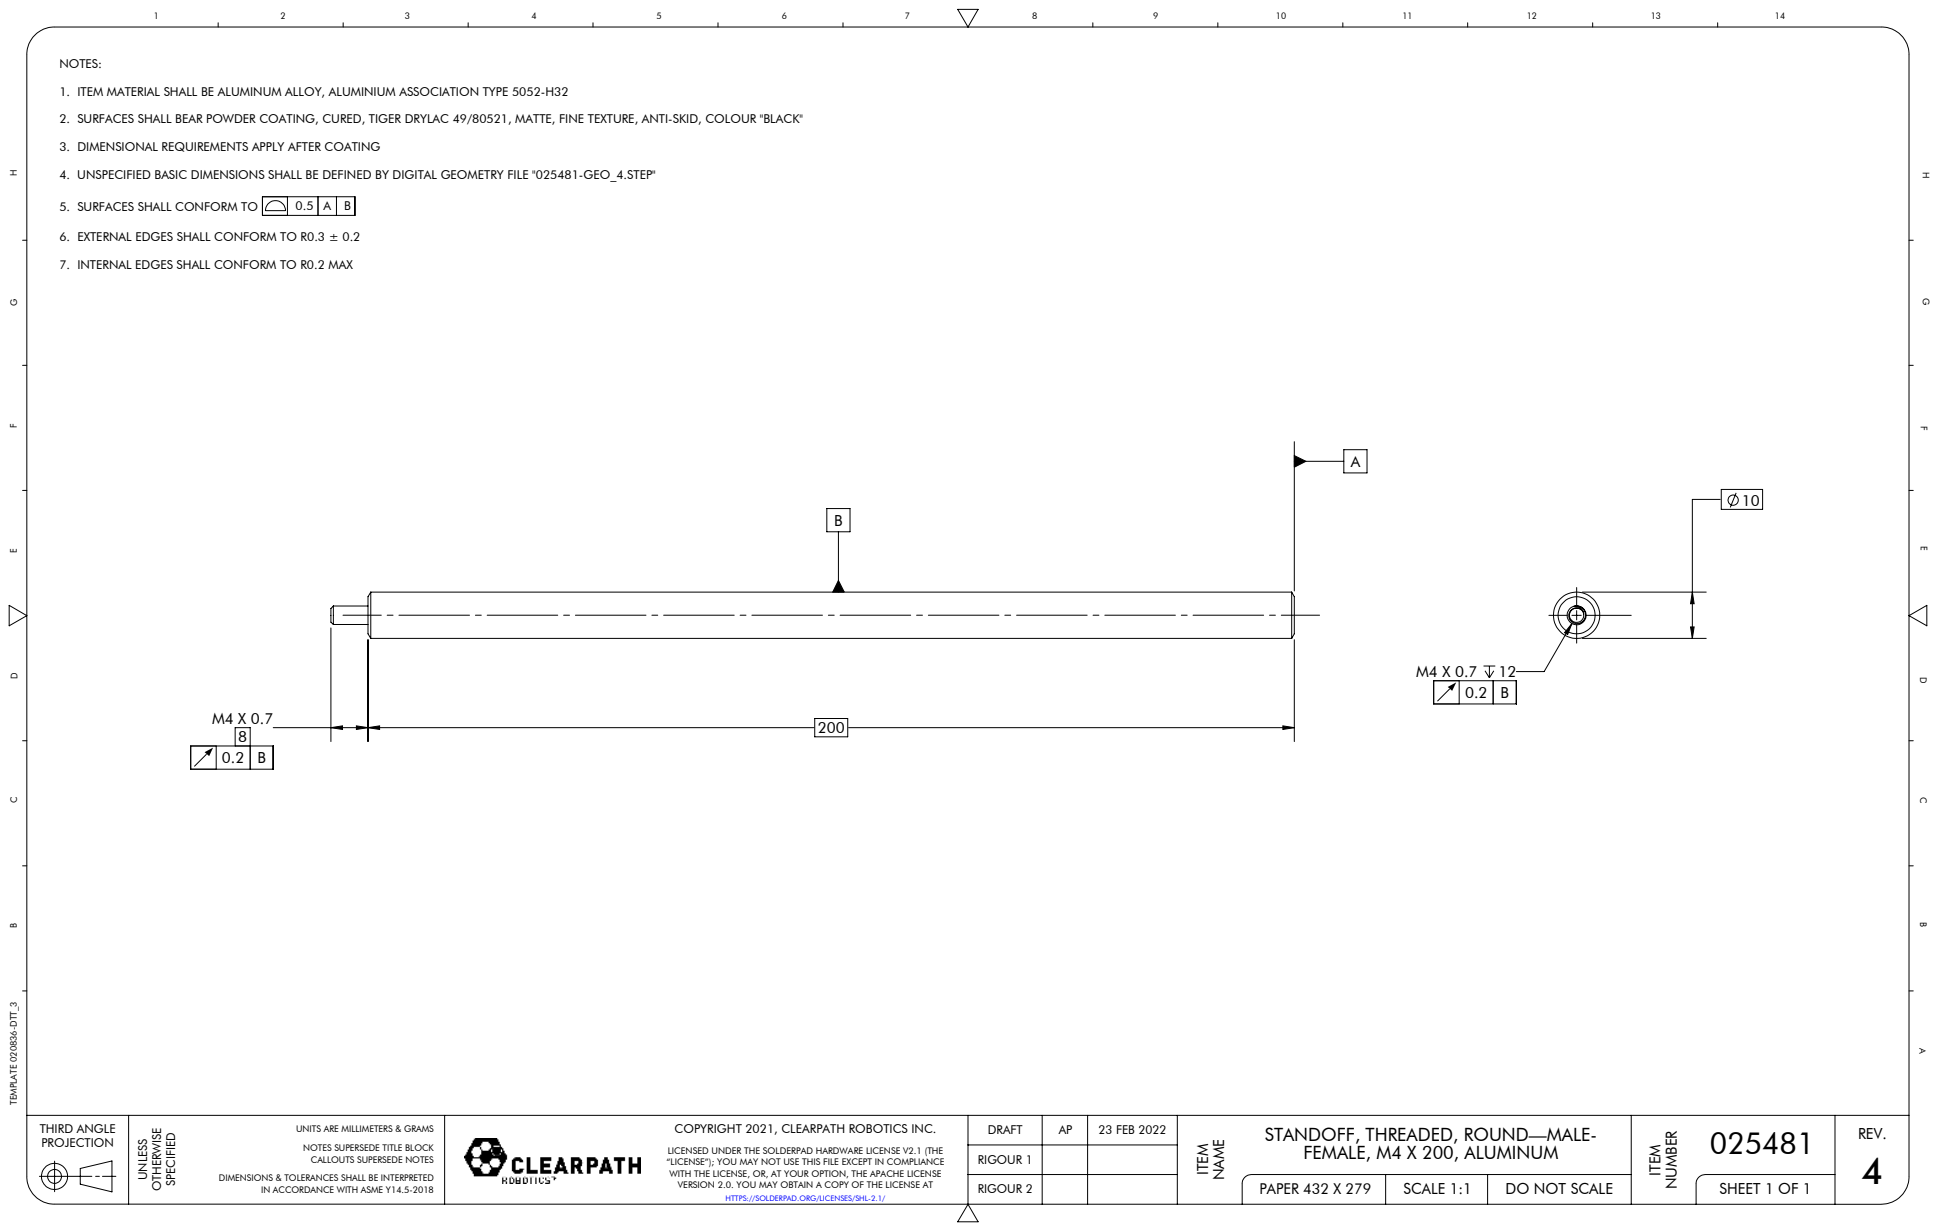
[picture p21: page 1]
5. SURFACES SHALL CONFORM TO; SCALE 1:1; SHEET 1 OF 1; THIRD ANGLE; PAPER 432 X 279; RIGOUR 1; RIGOUR 2; 23 FEB 2022; TEMPLATE 020836-DTT_3; IN ACCORDANCE WITH ASME Y14.5-2018; DO NOT SCALE

NOTES:
1. ITEM MATERIAL SHALL BE ALUMINUM ALLOY, ALUMINIUM ASSOCIATION TYPE 5052-H32
2. SURFACES SHALL BEAR POWDER COATING, CURED, TIGER DRYLAC 49/80521, MATTE, FINE TEXTURE, ANTI-SKID, COLOUR "BLACK"
3. DIMENSIONAL REQUIREMENTS APPLY AFTER COATING
4. UNSPECIFIED BASIC DIMENSIONS SHALL BE DEFINED BY DIGITAL GEOMETRY FILE "025481-GEO_4.STEP"

6. EXTERNAL EDGES SHALL CONFORM TO R0.3 ± 0.2
7. INTERNAL EDGES SHALL CONFORM TO R0.2 MAX

UNITS ARE MILLIMETERS & GRAMS
NOTES SUPERSEDE TITLE BLOCK
CALLOUTS SUPERSEDE NOTES

COPYRIGHT 2021, CLEARPATH ROBOTICS INC.

025481 STANDOFF, THREADED, ROUND—MALE-
FEMALE, M4 X 200, ALUMINUM

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

DIMENSIONS & TOLERANCES SHALL BE INTERPRETED

HTTPS://SOLDERPAD.ORG/LICENSES/SHL-2.1/

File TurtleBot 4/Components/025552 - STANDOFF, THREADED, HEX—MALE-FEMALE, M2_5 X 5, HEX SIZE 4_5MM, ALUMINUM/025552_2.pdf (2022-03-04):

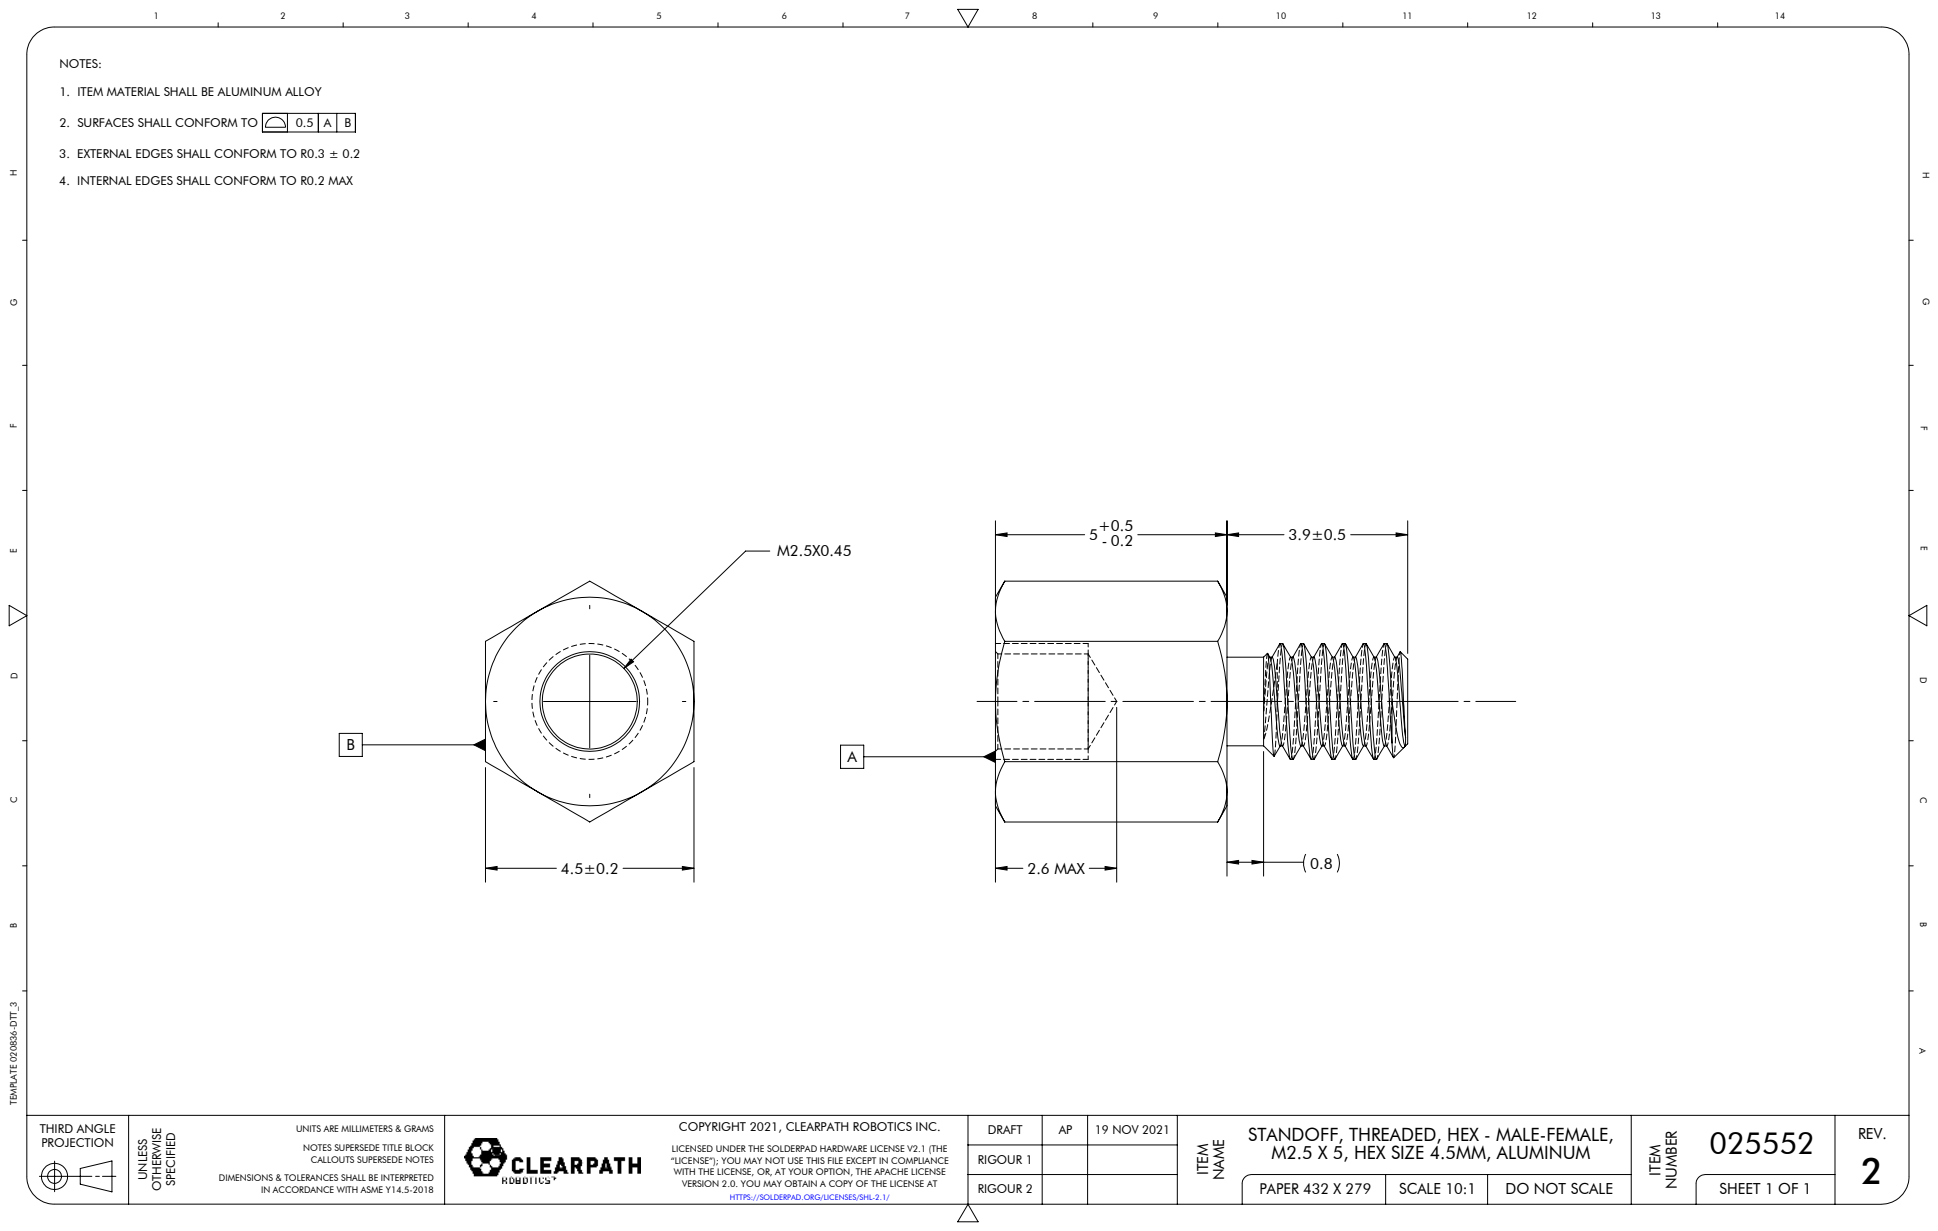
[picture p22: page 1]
0.8 2.6 MAX; 2. SURFACES SHALL CONFORM TO; SCALE 10:1; SHEET 1 OF 1; THIRD ANGLE; PAPER 432 X 279; RIGOUR 1; RIGOUR 2; 19 NOV 2021; TEMPLATE 020836-DTT_3; IN ACCORDANCE WITH ASME Y14.5-2018; DO NOT SCALE

NOTES:
1. ITEM MATERIAL SHALL BE ALUMINUM ALLOY

3. EXTERNAL EDGES SHALL CONFORM TO R0.3 ± 0.2
4. INTERNAL EDGES SHALL CONFORM TO R0.2 MAX

UNITS ARE MILLIMETERS & GRAMS
NOTES SUPERSEDE TITLE BLOCK
CALLOUTS SUPERSEDE NOTES

COPYRIGHT 2021, CLEARPATH ROBOTICS INC.

025552 STANDOFF, THREADED, HEX - MALE-FEMALE,
M2.5 X 5, HEX SIZE 4.5MM, ALUMINUM

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

DIMENSIONS & TOLERANCES SHALL BE INTERPRETED

HTTPS://SOLDERPAD.ORG/LICENSES/SHL-2.1/

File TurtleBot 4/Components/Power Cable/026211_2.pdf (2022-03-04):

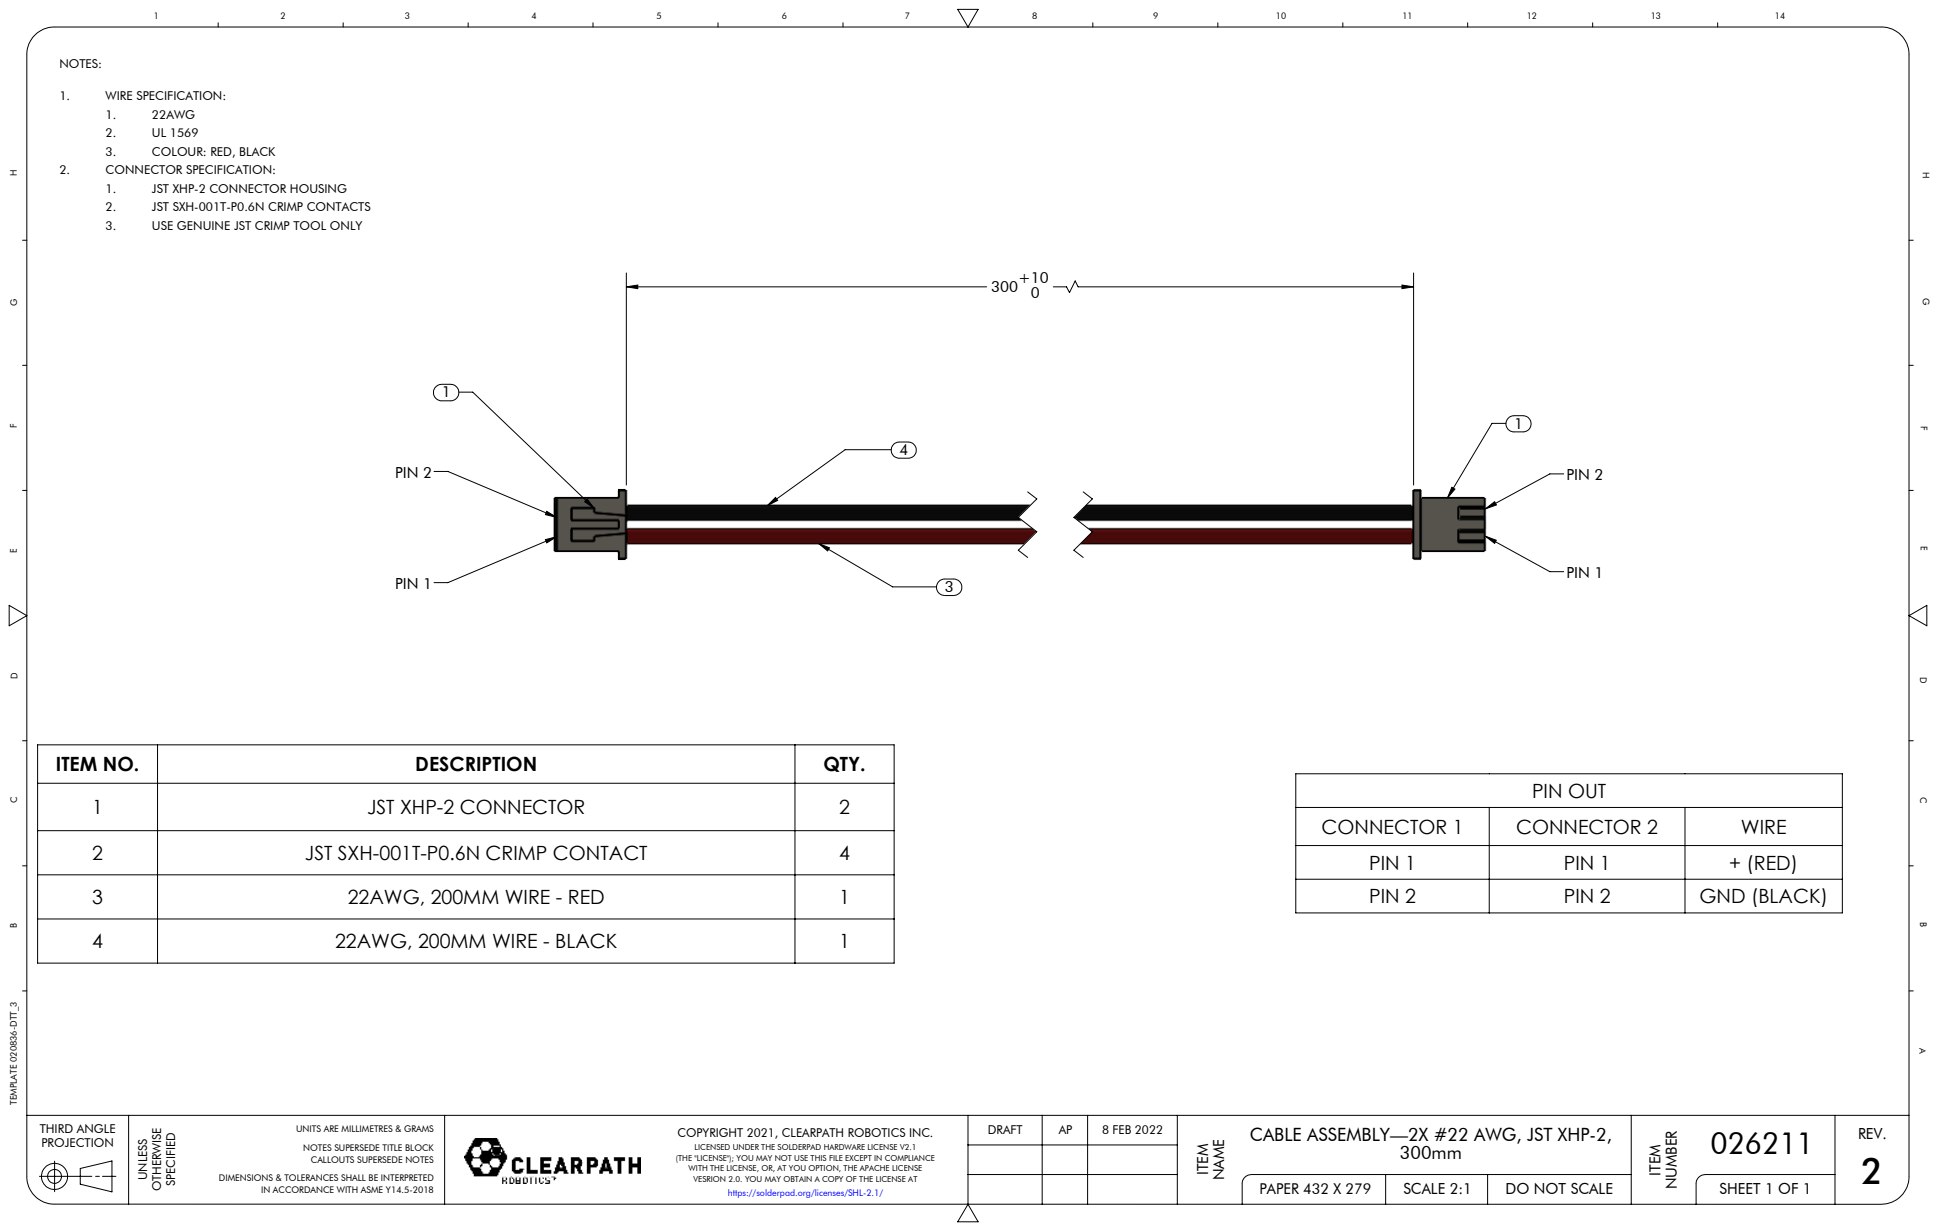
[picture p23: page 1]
PIN 1; PIN 2; 1. WIRE SPECIFICATION: 1. 22AWG 2. UL 1569 3. COLOUR: RED, BLACK 2. CONNECTOR SPECIFICATION:; 22AWG, 200MM WIRE - RED; 22AWG, 200MM WIRE - BLACK; PIN OUT; GND (BLACK); SCALE 2:1; SHEET 1 OF 1; THIRD ANGLE; PAPER 432 X 279; DRAFT; 8 FEB 2022; TEMPLATE 020836-DTT_3

1. JST XHP-2 CONNECTOR HOUSING
2. JST SXH-001T-P0.6N CRIMP CONTACTS
3. USE GENUINE JST CRIMP TOOL ONLY

ITEM NO. | DESCRIPTION | QTY.
1 | JST XHP-2 CONNECTOR | 2
2 | JST SXH-001T-P0.6N CRIMP CONTACT | 4

CONNECTOR 1 | CONNECTOR 2 | WIRE
PIN 1 | PIN 1 | + (RED)

UNITS ARE MILLIMETRES & GRAMS
NOTES SUPERSEDE TITLE BLOCK
CALLOUTS SUPERSEDE NOTES

COPYRIGHT 2021, CLEARPATH ROBOTICS INC.
LICENSED UNDER THE SOLDERPAD HARDWARE LICENSE V2.1
(THE "LICENSE"); YOU MAY NOT USE THIS FILE EXCEPT IN COMPLIANCE
WITH THE LICENSE, OR, AT YOU OPTION, THE APACHE LICENSE
VESRION 2.0. YOU MAY OBTAIN A COPY OF THE LICENSE AT

026211 CABLE ASSEMBLY—2X #22 AWG, JST XHP-2,

DIMENSIONS & TOLERANCES SHALL BE INTERPRETED

IN ACCORDANCE WITH ASME Y14.5-2018

https://solderpad.org/licenses/SHL-2.1/

DO NOT SCALE

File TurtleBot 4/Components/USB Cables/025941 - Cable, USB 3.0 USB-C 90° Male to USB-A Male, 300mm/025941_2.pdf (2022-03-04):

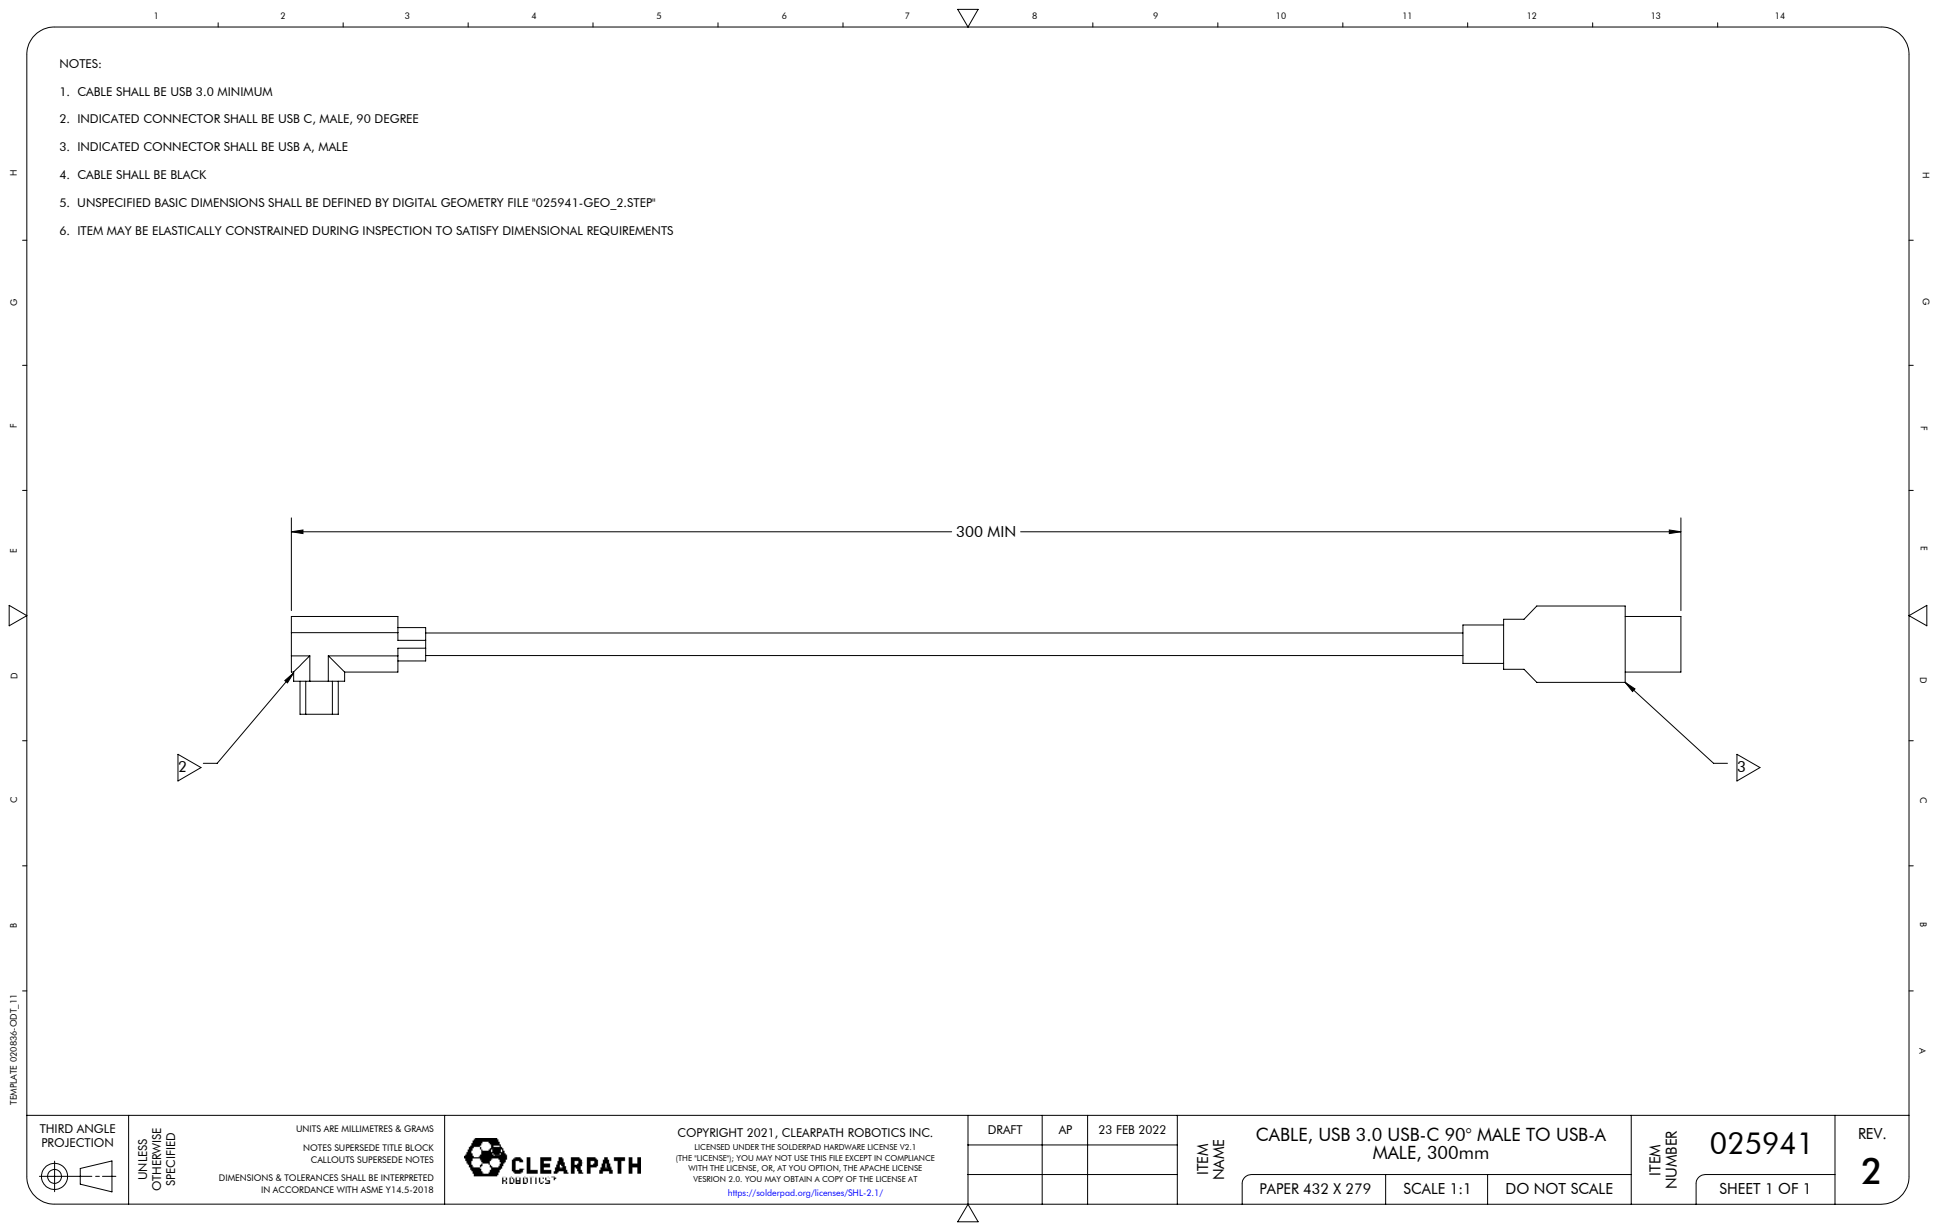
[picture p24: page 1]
300 MIN; SCALE 1:1; SHEET 1 OF 1; THIRD ANGLE; PAPER 432 X 279; MALE, 300mm; DRAFT; 23 FEB 2022; TEMPLATE 020836-ODT_11

NOTES:
1. CABLE SHALL BE USB 3.0 MINIMUM
2. INDICATED CONNECTOR SHALL BE USB C, MALE, 90 DEGREE
3. INDICATED CONNECTOR SHALL BE USB A, MALE
4. CABLE SHALL BE BLACK
5. UNSPECIFIED BASIC DIMENSIONS SHALL BE DEFINED BY DIGITAL GEOMETRY FILE "025941-GEO_2.STEP"
6. ITEM MAY BE ELASTICALLY CONSTRAINED DURING INSPECTION TO SATISFY DIMENSIONAL REQUIREMENTS

UNITS ARE MILLIMETRES & GRAMS
NOTES SUPERSEDE TITLE BLOCK
CALLOUTS SUPERSEDE NOTES

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

025941 CABLE, USB 3.0 USB-C 90° MALE TO USB-A

DIMENSIONS & TOLERANCES SHALL BE INTERPRETED

IN ACCORDANCE WITH ASME Y14.5-2018

https://solderpad.org/licenses/SHL-2.1/

DO NOT SCALE

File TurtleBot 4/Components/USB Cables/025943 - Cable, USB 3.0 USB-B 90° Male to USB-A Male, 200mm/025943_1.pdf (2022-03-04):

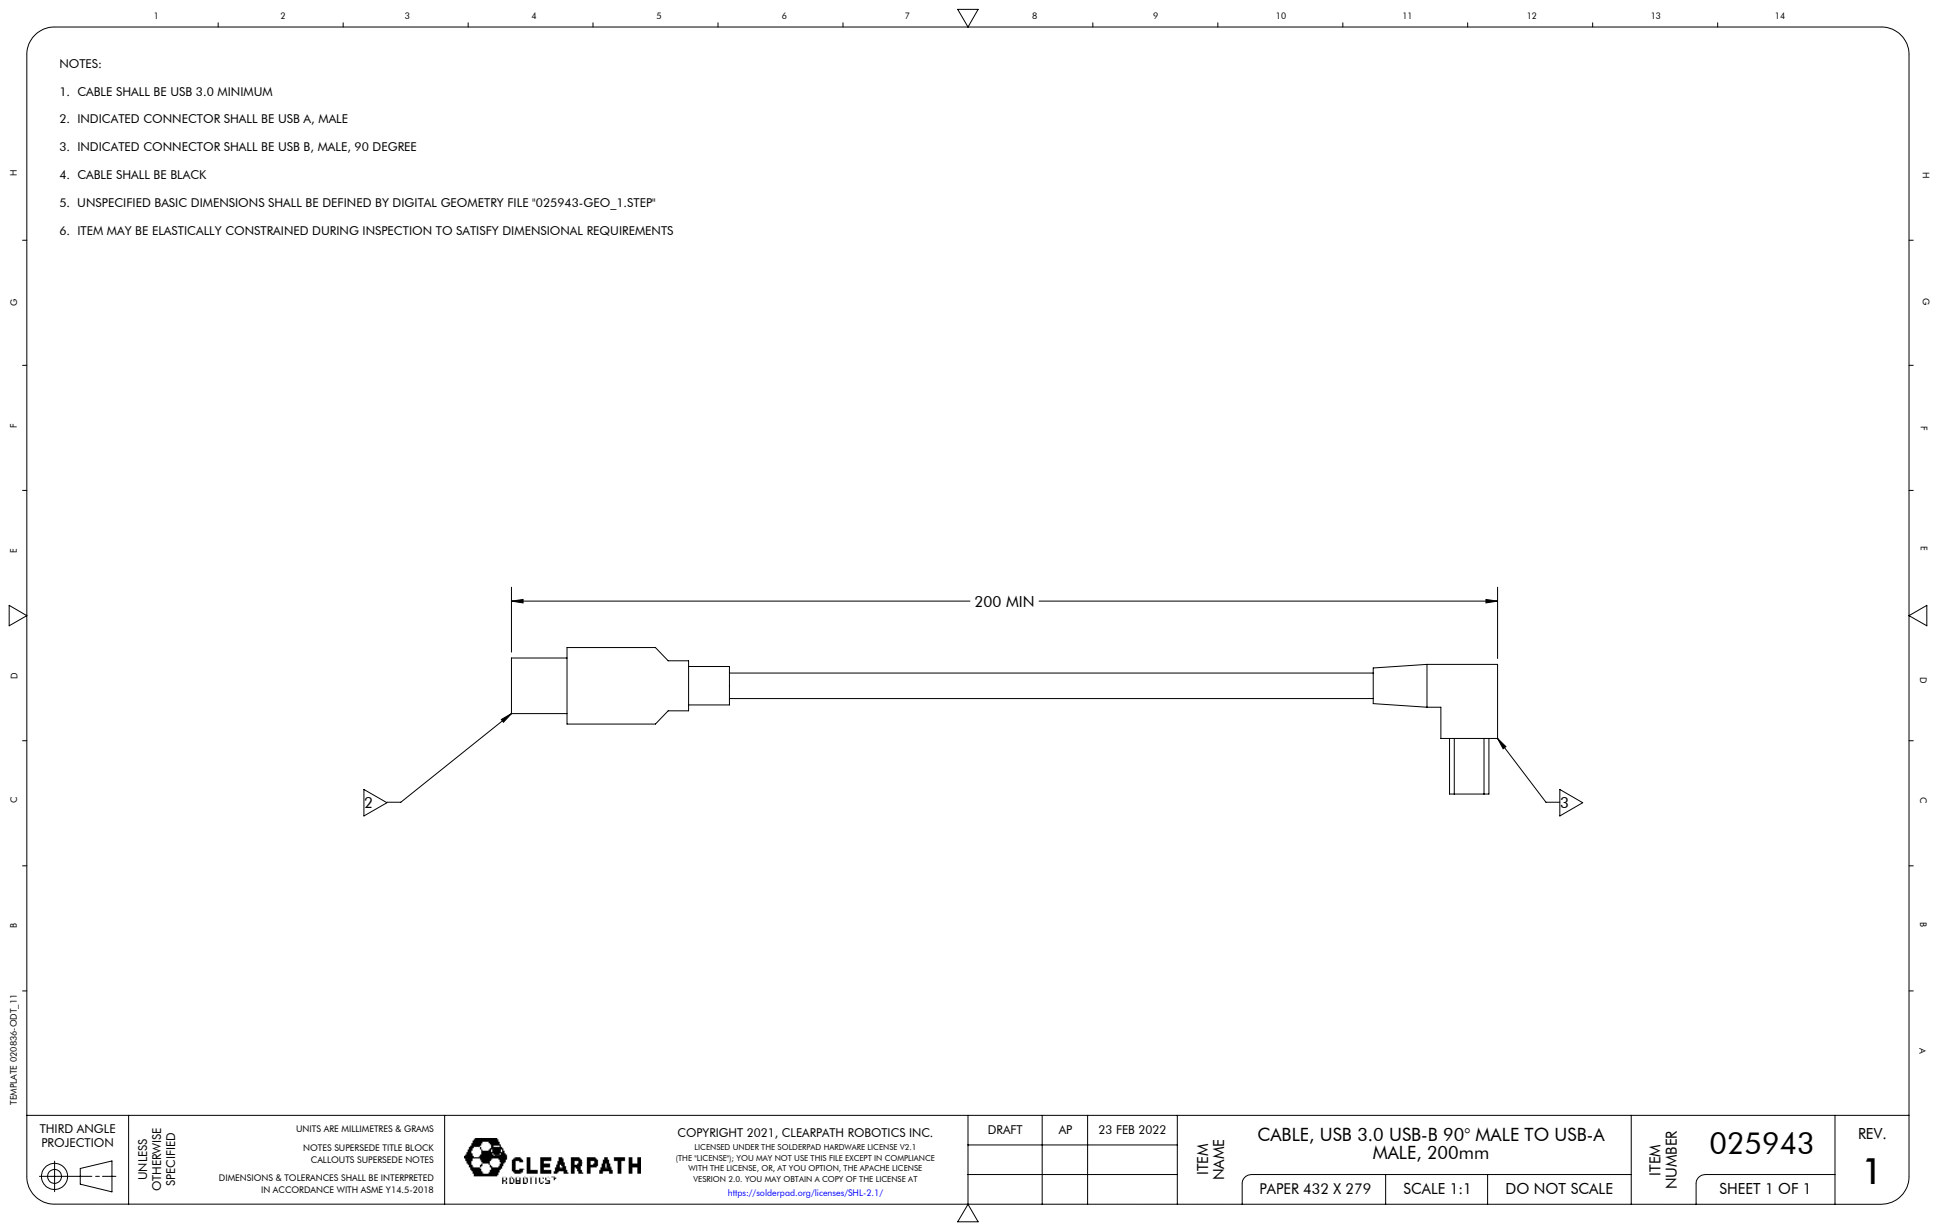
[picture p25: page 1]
200 MIN; 1 SCALE 1:1; SHEET 1 OF 1; THIRD ANGLE; PAPER 432 X 279; MALE, 200mm; DRAFT; 23 FEB 2022; TEMPLATE 020836-ODT_11

NOTES:
1. CABLE SHALL BE USB 3.0 MINIMUM
2. INDICATED CONNECTOR SHALL BE USB A, MALE
3. INDICATED CONNECTOR SHALL BE USB B, MALE, 90 DEGREE
4. CABLE SHALL BE BLACK
5. UNSPECIFIED BASIC DIMENSIONS SHALL BE DEFINED BY DIGITAL GEOMETRY FILE "025943-GEO_1.STEP"
6. ITEM MAY BE ELASTICALLY CONSTRAINED DURING INSPECTION TO SATISFY DIMENSIONAL REQUIREMENTS

UNITS ARE MILLIMETRES & GRAMS
NOTES SUPERSEDE TITLE BLOCK
CALLOUTS SUPERSEDE NOTES

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

025943 CABLE, USB 3.0 USB-B 90° MALE TO USB-A

DIMENSIONS & TOLERANCES SHALL BE INTERPRETED

IN ACCORDANCE WITH ASME Y14.5-2018

https://solderpad.org/licenses/SHL-2.1/

DO NOT SCALE

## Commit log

2022-03-04 Initial upload
    [025394-FLAT_3.DXF, 025394-GEO_3.STEP, 025426-FLAT_6.DXF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]
2022-03-04 Added OAK-D cameras Added Turtlebot4 renders
2023-01-26 Standard Assembly Update
    Updated the mechanical assembly and BOM. Changed the fastening method for the R-PI to the base robot. Replaced the M-F standoffs with F-F standoffs and fastening with screws from both sides now. Allows for easier assembly.
2023-01-26 Created TTB4 Lite Adapter Plate
    Created the TTB4 Lite adapter plate. Adapter plates allow users to mount additional hardware to the top of the base robot without making modifications.
    [Adapter Plate, Turtlebot4 Lite, Left Side—Plastic, 3D Printed.SLDPRT, Adapter Plate, Turtlebot4 Lite, Left Side—Plastic, 3D Printed.STL, Adapter Plate, Turtleb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]
2023-07-07 Addition of PCBA Files
    Added files under \TurtleBot 4\Components\025618 - PCBA, SHELL-SHAPE—Ø273 X 230 for PCBA.
